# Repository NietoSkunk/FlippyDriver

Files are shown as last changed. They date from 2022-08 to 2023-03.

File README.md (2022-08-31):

# FlippyDriver

Driver board for Luminator MAX3000 Flip Dot Panels, allowing for chaining multiple panels, 3.3V and 5V tolerant inputs, and LED illumination with PWM dimming.

[Get it on PCBWay!](https://www.pcbway.com/project/shareproject/Luminator_MAX3000_Driver_Board_04b50fe9.html)

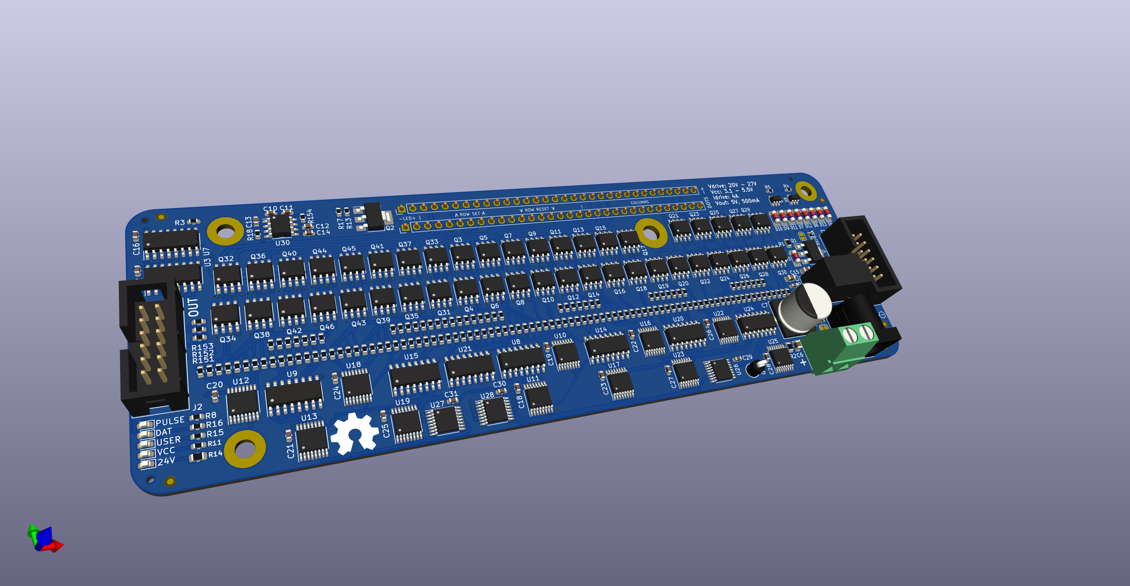
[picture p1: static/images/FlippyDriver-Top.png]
top

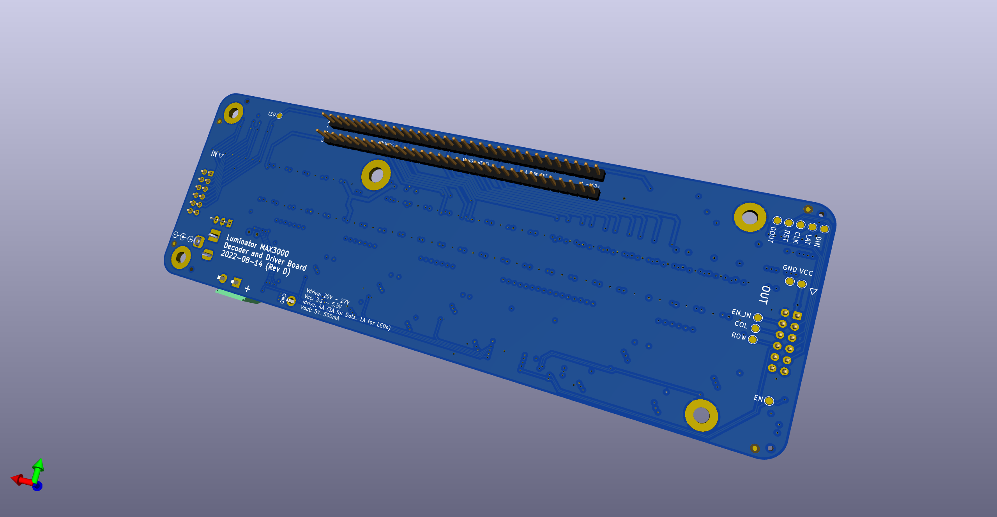
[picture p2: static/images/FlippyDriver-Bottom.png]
bottom

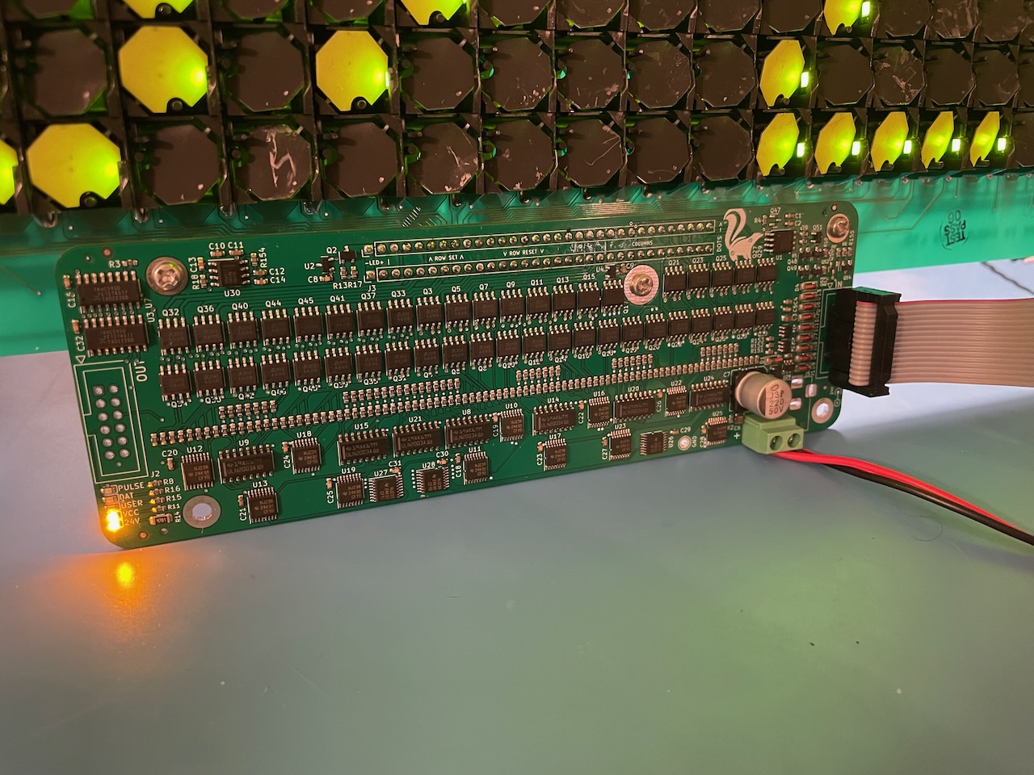
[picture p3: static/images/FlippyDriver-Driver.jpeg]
driver board

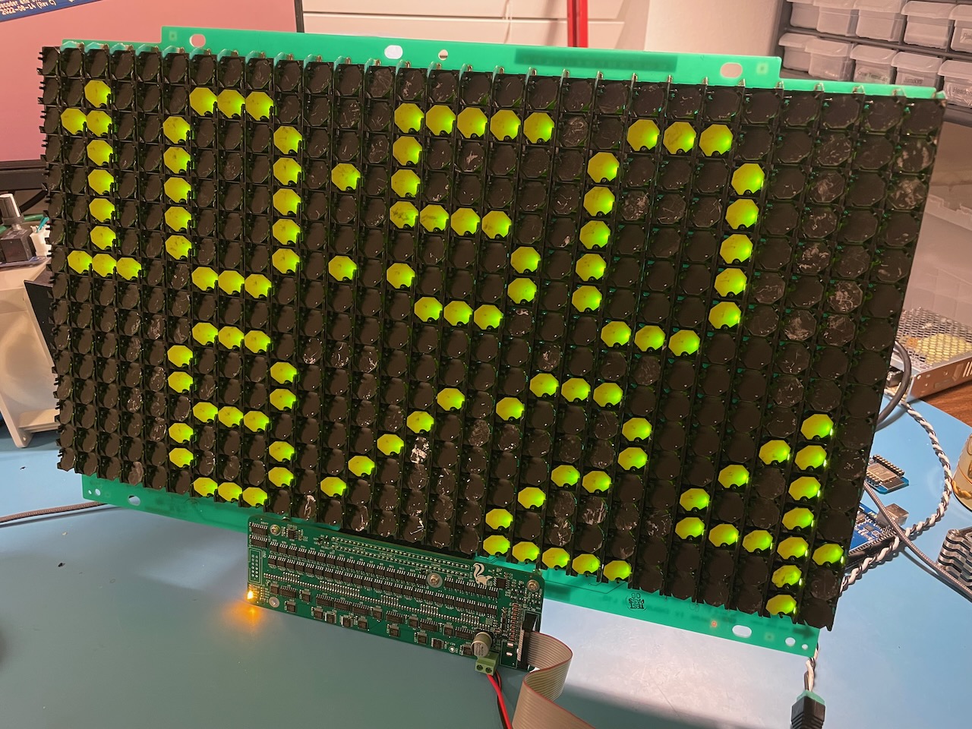
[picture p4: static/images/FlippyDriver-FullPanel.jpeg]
full panel


## Cloning repository (with Submodules)

```bash
$ git clone --recurse-submodules git@github.com:NietoSkunk/FlippyDriver.git
```

## Production notes

* 4 Layer board, preferably at least TG155. The display traces get warm when running at full tilt, and proper ventilation and thermal management is recommended.
* Several components are marked as DNI and are not necessary to populate. 
* F1, F2, and U30 have solder jumpers to bypass if they are not populated.
* Two mounting holes are in line with the holes on the panel, and support a 10mm M3 standoff. The larger mounting hole in the middle of the mouard matches with the hole on the panel, and supports a 10mm M4 standoff.
* The 7805 5V Aux Output is compatible with both a VX7805-500 switching regulator module and a L7805 linear regulator (heatsink recommended).

## Associated projects

* [FlippyAdapter - Panel Header to IDE Ribbon Cables](https://github.com/NietoSkunk/FlippyAdapter)
* [FlippyControl - Arduino / ESP32 Shield](https://github.com/NietoSkunk/FlippyControl)

## Data Harness

| Pin | # | # | Pin |
| --- | - | - | --- |
| VCC | 1 | 2 | GND |
| MOSI | 3 | 4 | PULSE_ENABLE |
| LATCH | 5 | 6 | COL_PULSE_N |
| CLK | 7 | 8 | ROW_PULSE_N |
| RESET | 9 | 10 | LED PWM |
| 5V Return | 11 | 12 | GND |

All logic circuitry is both 3.3V and 5V tolerant, as long as the VCC power rail is at least as high as the logic voltage. The RESET line has a pull-down resistor and is Active-Low. The PULSE_ENABLE pin is active high (i.e. pulse on high level), and the COL and ROW PULSE pins are active low (i.e. pulse on low level). 

WARNING: The low side sink drivers must be turned on after the high side, and turned off before the high side. For example, a pulse sequence of ROW Low, COL Low, COL High, ROW High would be used if the row is sourced and the column is grounded in order to set a bit. Damage may occur to the circuit if this order is not maintained!

The 5V Return pin is connected to the output of the 7805 regulator, which allows a board to receive 5V power from the 24V drive power.  It is not passed through to other modules, and thus only the first board in the chain has an accessible 5V output. All other boards in the chain do not have the aux output routed anywhere, and they can optionally be depopulated.

## Board Harness

| Pin | # | # | Pin |
| --- | - | - | --- |
| LED- | 1 | 2 | LED- |
| LED+ | 3 | 4 | LED+ |
| ROW_2_RESET | 5 | 6 | ROW_2_SET |
| ROW_4_RESET | 7 | 8 | ROW_4_SET |
| ROW_6_RESET | 9 | 10 | ROW_6_SET |
| ROW_8_RESET | 11 | 12 | ROW_8_SET |
| ROW_10_RESET | 13 | 14 | ROW_10_SET |
| ROW_12_RESET | 15 | 16 | ROW_12_SET |
| ROW_14_RESET | 17 | 18 | ROW_14_SET |
| ROW_16_RESET | 19 | 20 | ROW_16_SET |
| ROW_15_RESET | 21 | 22 | ROW_15_SET |
| ROW_13_RESET | 23 | 24 | ROW_13_SET |
| ROW_11_RESET | 25 | 26 | ROW_11_SET |
| ROW_9_RESET | 27 | 28 | ROW_9_SET |
| ROW_7_RESET | 29 | 30 | ROW_7_SET |
| ROW_5_RESET | 31 | 32 | ROW_5_SET |
| ROW_3_RESET | 33 | 34 | ROW_3_SET |
| ROW_1_RESET | 35 | 36 | ROW_1_SET |
| COL_2 | 37 | 38 | COL_1 |
| COL_4 | 39 | 40 | COL_3 |
| COL_6 | 41 | 42 | COL_5 |
| COL_8 | 43 | 44 | COL_7 |
| COL_10 | 45 | 46 | COL_9 |
| COL_12 | 47 | 48 | COL_11 |
| COL_14 | 49 | 50 | COL_13 |
| COL_16 | 51 | 52 | COL_15 |
| COL_18 | 53 | 54 | COL_17 |
| COL_20 | 55 | 56 | COL_19 |
| COL_22 | 57 | 58 | COL_21 |
| COL_24 | 59 | 60 | COL_23 |
| COL_26 | 61 | 62 | COL_25 |
| COL_28 | 63 | 64 | COL_27 |

## LEDs

  * PULSE: Illuminated when the PULSE_ENABLE pin is high.
  * DAT: Illuminates when data is being clocked into the shift register.
  * USER: Programmable LED connected to bit 12 of the shift register.
  * VCC: Illuminated when the VCC power rail is present.
  * 24V: Illuminated when the 24V power rail is present.

## Shift Register

Each board contains a pair of 74HC595 shift registers, which are used to select a single pixel to be enabled at a time. This can be driven either directly with GPIO outputs, or using a hardware SPI output. The format of the data is MSB first, clock on high.

The Row and Column decoders are grouped into banks of eight, using 74HC238 3:8 decoders. The Column and Row A2/A1/A0 lines select the output of each bank, and the Column and Row Bank lines select which bank is active. The Row and Column source line switches that output to drive a high side source instead of a low side sink.

The I2C Pullup line is used to enable a set of 4.7kOhm resistors on the I2C bus, which allows a single board in a chain to optionally provide pullups.

The output of the shift register is sent out to the OUT header, and comes in to the next board in the chain on the MOSI line. This allows multiple boards to be controlled at once by shifting 16 bits of data for each board.

| Bit | Function |
| --- | --- |
|  0  | Column A2 |
|  1  | Column A1 |
|  2  | Column A0 |
|  3  | Row A0 |
|  4  | Row A1 |
|  5  | Row A2 |
|  6  | Row Bank |
|  7  | Column Bank 0 |
|  8  | Column Source |
|  9  | N/C |
|  10 | Row Source |
|  11 | Row Bank |
|  12 | N/C |
|  13 | User LED |
|  14 | N/C |
|  15 | N/C |

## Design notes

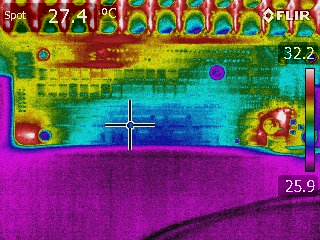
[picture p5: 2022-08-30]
static/images/Thermals_1.jpg

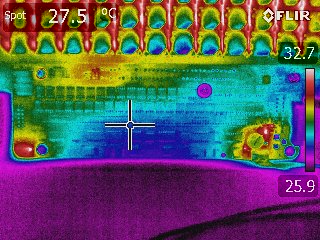
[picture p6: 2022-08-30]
static/images/Thermals_2.jpg

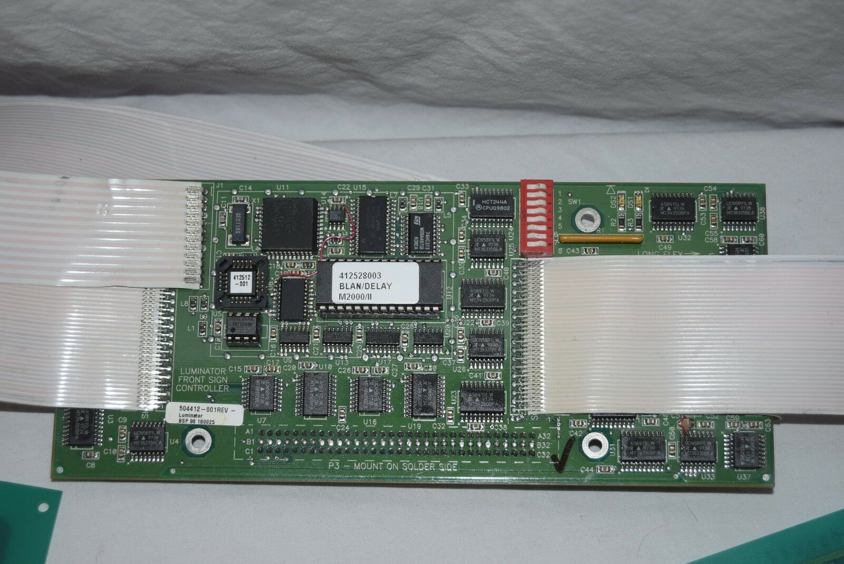
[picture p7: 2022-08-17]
Reference/s-l1600.jpg

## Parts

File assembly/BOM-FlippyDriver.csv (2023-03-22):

Comment | Designator | Footprint | LCSC
220u | C4 | CP_Elec_10x10 | C125977
0.1u | C10,C16,C18,C19,C2,C20,C21,C22,C23,C24,C25,C26,C27,C28,C29,C30,C31,C32,C33,C36,C37,C38,C5,C6,C7,C9 | C_0603_1608Metric | C14663
AO3401A | Q1,Q2,Q47,Q48,Q53 | SOT-23 | C15127
1u | C11,C12,C34 | C_0603_1608Metric | C15849
10k | R14,R3,R9 | R_0805_2012Metric | C17414
500mA | F2 | Fuse_0603_1608Metric | C206959
AO3400A | Q49,Q50,Q51,Q52,Q54,Q55 | SOT-23 | C20917
1k | R100,R101,R102,R119,R120,R121,R122,R123,R124,R125,R126,R13,R143,R144,R145,R146,R147,R148,R149,R150,R153,R35,R36,R37,R38,R39,R40,R41,R42,R59,R60,R61,R62,R63,R64,R65,R66,R83,R84,R85,R86,R87,R88,R89,R90,R99 | R_0603_1608Metric | C21190
2.4k,1% | R12,R159,R160 | R_0603_1608Metric | C22940
220R | R11,R15,R2,R8 | R_0603_1608Metric | C22962
5.6k,1% | R16 | R_0603_1608Metric | C23189
56k | R1,R10,R17,R4,R5,R6,R7 | R_0603_1608Metric | C23206
10k | R103,R104,R105,R106,R107,R108,R109,R110,R111,R112,R113,R114,R115,R116,R117,R118,R127,R128,R129,R130,R131,R132,R133,R134,R135,R136,R137,R138,R139,R140,R141,R142,R151,R152,R154,R155,R156,R157,R158,R161,R18,R19,R20,R21,R22,R23,R24,R25,R26,R27,R28,R29,R30,R31,R32,R33,R34,R43,R44,R45,R46,R47,R48,R49,R50,R51,R52,R53,R54,R55,R56,R57,R58,R67,R68,R69,R70,R71,R72,R73,R74,R75,R76,R77,R78,R79,R80,R81,R82,R91,R92,R93,R94,R95,R96,R97,R98 | R_0603_1608Metric | C25804
1u | C1 | C_0805_2012Metric | C28323
4.7u | C8 | C_1206_3216Metric | C29823
SMAJ33CA | D5 | D_SMA | C3019524
CJ431 | U2 | SOT-23 | C3113
AP4606 | Q10,Q11,Q12,Q13,Q14,Q15,Q16,Q17,Q18,Q19,Q20,Q21,Q22,Q23,Q24,Q25,Q26,Q27,Q28,Q29,Q3,Q30,Q31,Q32,Q33,Q34,Q35,Q36,Q37,Q38,Q39,Q4,Q40,Q41,Q42,Q43,Q44,Q45,Q46,Q5,Q6,Q7,Q8,Q9 | SOIC-8_3.9x4.9mm_P1.27mm | C353084
74HC238 | U10,U11,U12,U13,U16,U17,U18,U19,U22,U23,U25,U26,U27,U28 | TSSOP-16_4.4x5mm_P0.65mm | C403724
MCP9700T-ETT | U29,U6 | SOT-23 | C42288
10u | C15,C17,C3,C35 | C_0805_2012Metric | C440198
5A | F1 | Fuse_0603_1608Metric | C553915
0.01u | C13,C14 | C_0603_1608Metric | C57112
74HC595 | U3,U7 | SOIC-16_3.9x9.9mm_P1.27mm | C5947
19-213/Y2C-CQ2R2L/3T(CY) | D14,D3 | LED_0603_1608Metric | C72038
19-217/BHC-ZL1M2RY/3T | D15 | LED_0603_1608Metric | C72041
19-217/GHC-YR1S2/3T | D2 | LED_0603_1608Metric | C72043
ULN2003ADR | U14,U15,U20,U21,U24,U8,U9 | SOIC-16_3.9x9.9mm_P1.27mm | C7512
NE555D | U30 | SOIC-8_3.9x4.9mm_P1.27mm | C7593
LM393 | U1,U5 | SOIC-8_3.9x4.9mm_P1.27mm | C7955
ZMM5V6 | D1,D10,D11,D12,D13,D16,D17,D4,D6,D7,D8,D9 | D_MiniMELF | C8062
NCD0805R1 | D18 | LED_0805_2012Metric | C84256
MountingHole_Pad | H1 | MountingHole_3.5mm_Pad_TopBottom
MountingHole_Pad | H2 | MountingHole_3.5mm_Pad_TopBottom
MountingHole_Pad | H4 | MountingHole_3.5mm_Pad_TopBottom
MountingHole_Pad | H5 | MountingHole_4.5mm_Pad_TopBottom
MountingHole_Pad | H3 | MountingHole_3.5mm_Pad_TopBottom
24V Input | J5 | BarrelJack_Horizontal
GND | TP6 | TestPoint_Keystone_5005-5009_Compact
Board Harness | J3 | Luminator_MAX3000
Data Harness In | J1 | IDC-Header_2x06_P2.54mm_Vertical
Data Harness Out | J2 | IDC-Header_2x06_P2.54mm_Vertical
LAT | TP12 | TestPoint_Pad_D1.5mm
DIN | TP11 | TestPoint_Pad_D1.5mm
COL | TP15 | TestPoint_Pad_D1.5mm
RST | TP2 | TestPoint_Pad_D1.5mm
VCC | TP4 | TestPoint_Pad_D1.5mm
EN | TP13 | TestPoint_Pad_D1.5mm
EN_IN | TP7 | TestPoint_Pad_D1.5mm
ROW | TP14 | TestPoint_Pad_D1.5mm
DOUT | TP3 | TestPoint_Pad_D1.5mm
CLK | TP1 | TestPoint_Pad_D1.5mm
GND | TP5 | TestPoint_Pad_D1.5mm
LED | TP10 | TestPoint_Pad_D1.5mm
VX7805-500 | U4 | Converter_DCDC_RECOM_R-78E-0.5_THT
24V Input | J4 | TerminalBlock_Phoenix_MKDS-1,5-2_1x02_P5.00mm_Horizontal

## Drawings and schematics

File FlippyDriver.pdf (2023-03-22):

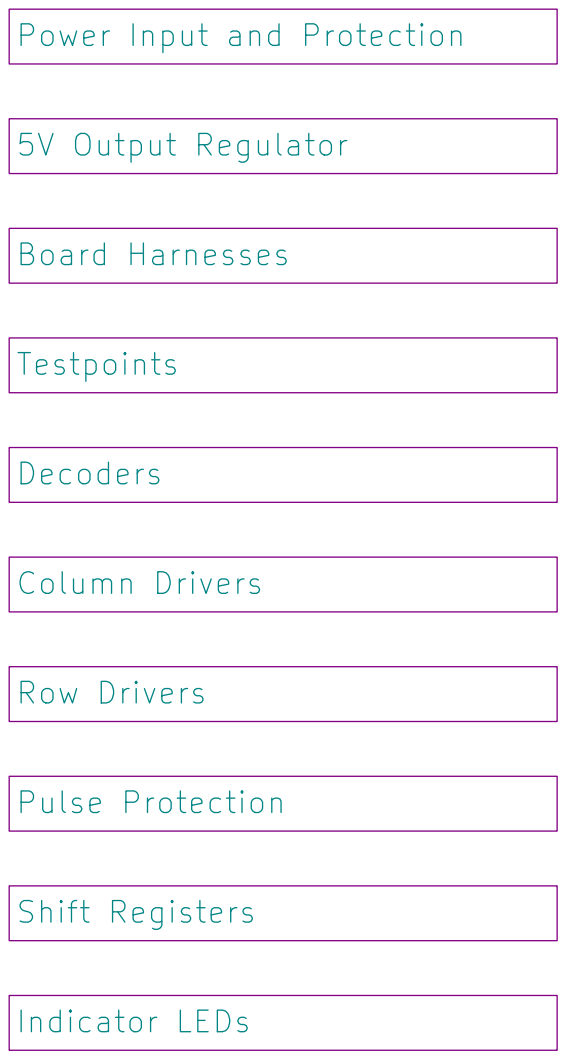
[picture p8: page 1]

Power Input and Protection

File: FlippyDriver.kicad_sch Sheet: / Row Drivers

Id: 1/11 Title: Luminator MAX3000 Custom Driver Board

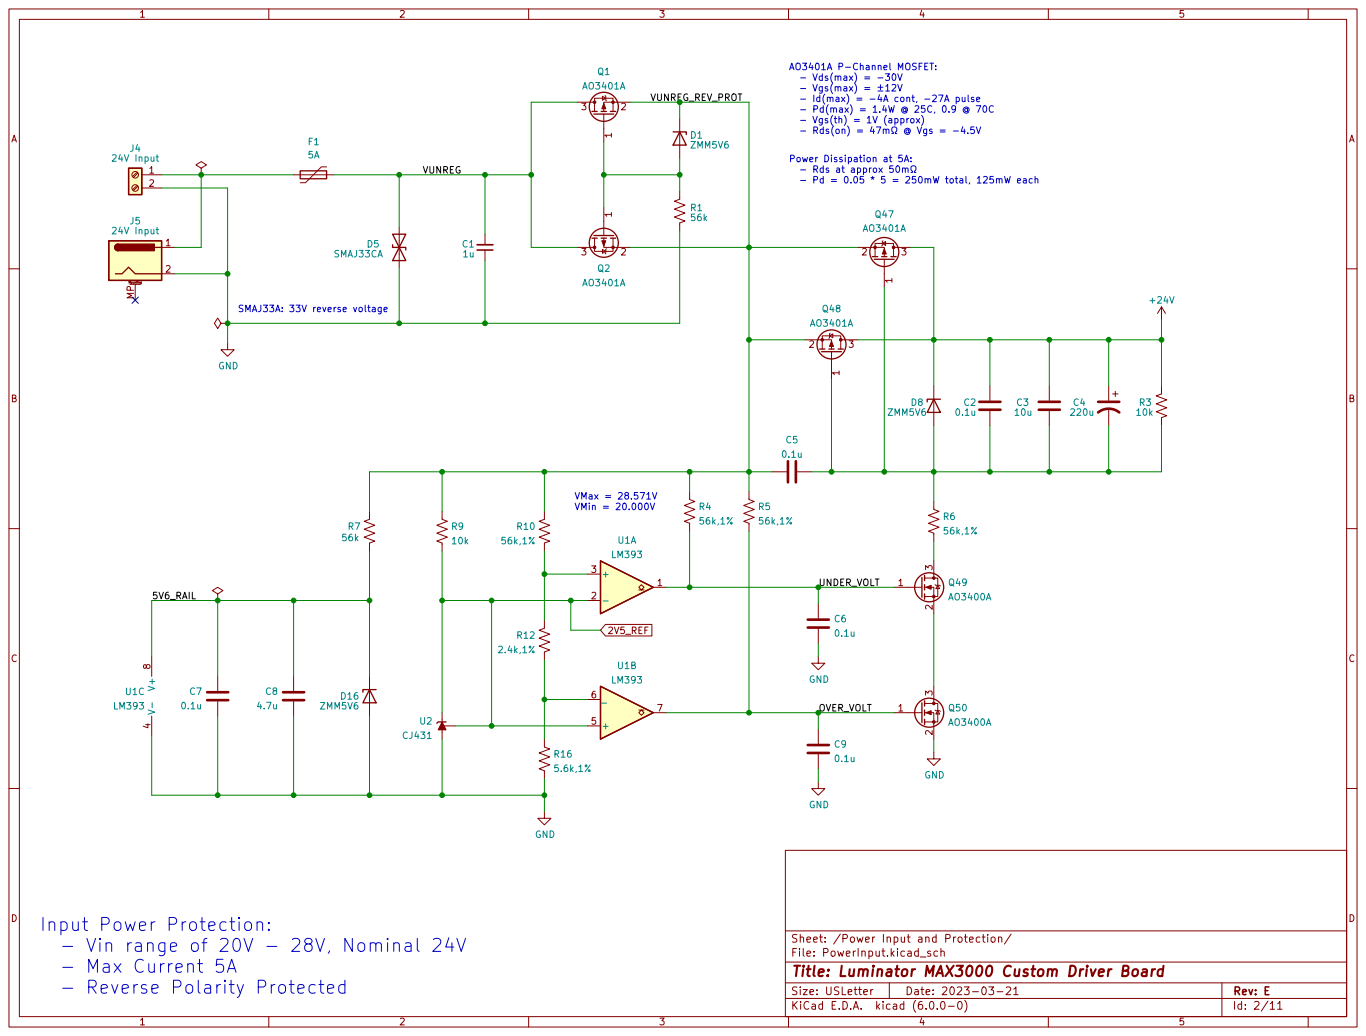
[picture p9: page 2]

- Vds(max) = -30V
- Id(max) = -4A cont, -27A pulse
- Pd(max) = 1.4W @ 25C, 0.9 @ 70C
- Vgs(th) = 1V (approx)

Sheet: /Power Input and Protection/ C6
0.1u GND

Input Power Protection:
- Vin range of 20V - 28V, Nominal 24V
- Max Current 5A
- Reverse Polarity Protected

File: PowerInput.kicad_sch
Id: 2/11 Title: Luminator MAX3000 Custom Driver Board

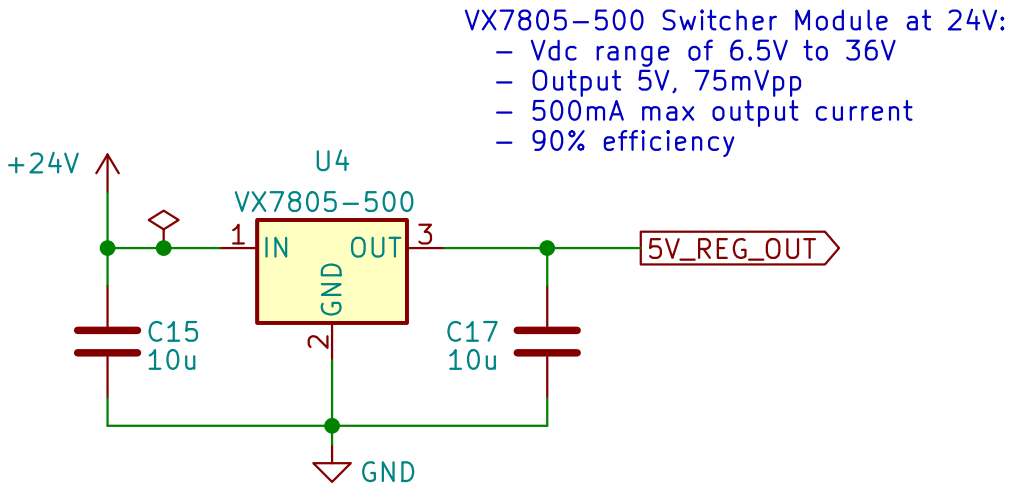
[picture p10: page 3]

5V_REG_OUT VX7805-500 Switcher Module at 24V:
- Vdc range of 6.5V to 36V
- Output 5V, 75mVpp
- 500mA max output current
- 90% efficiency

Sheet: /5V Output Regulator/ GND

File: 5V_Reg.kicad_sch
Id: 3/11 Title: Luminator MAX3000 Custom Driver Board

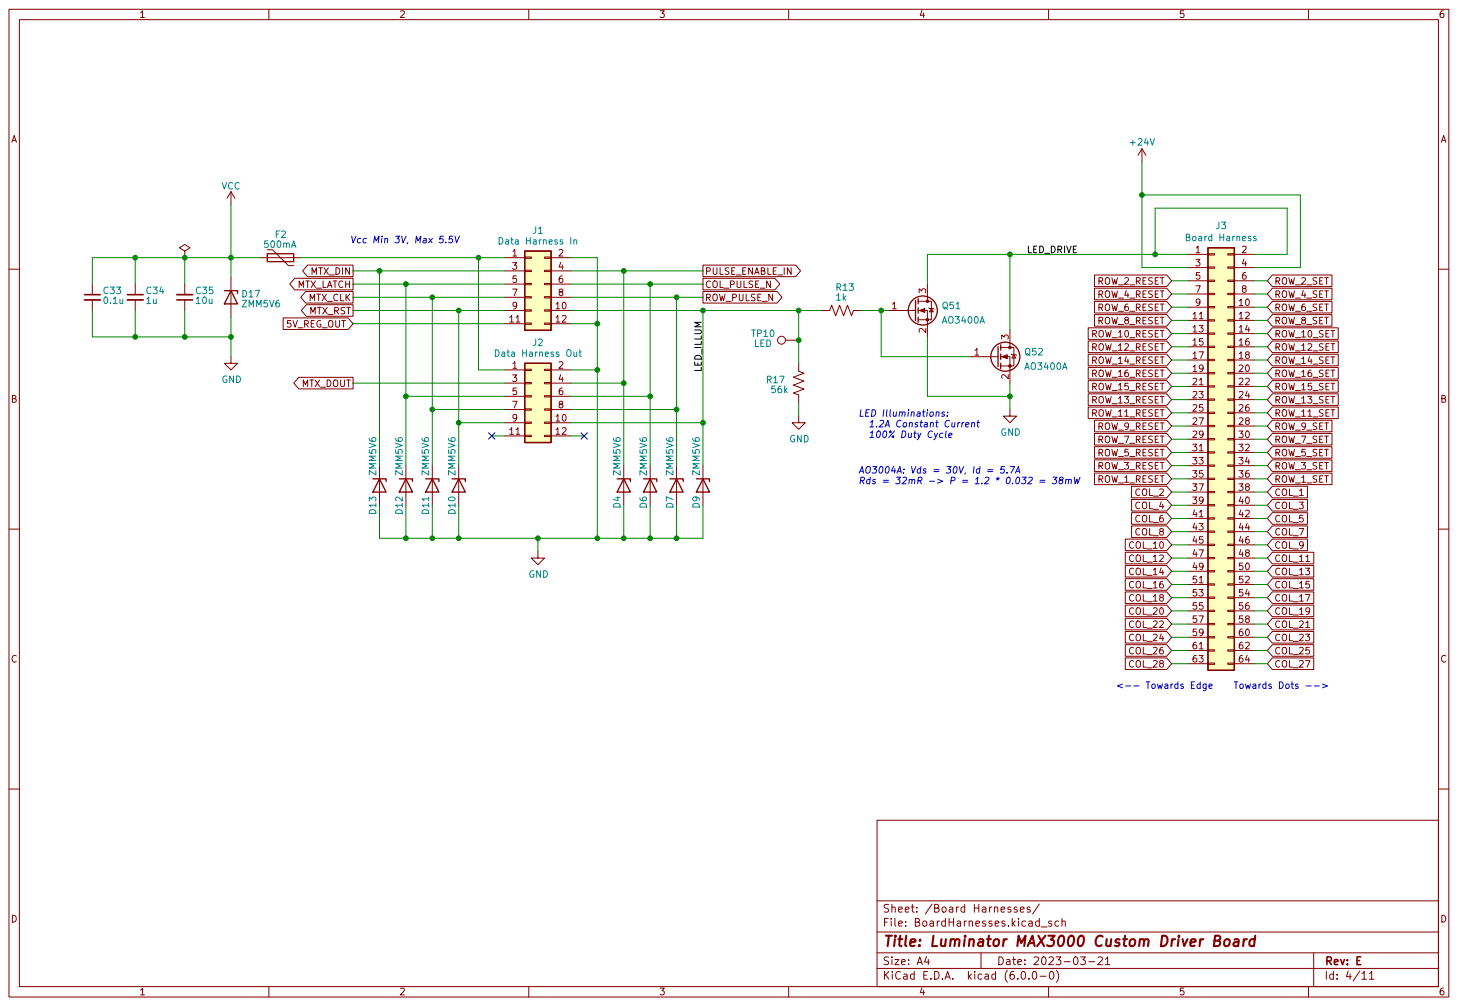
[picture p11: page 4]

9 | | 10

File: BoardHarnesses.kicad_sch Sheet: /Board Harnesses/ GND

<-- Towards Edge Towards Dots -->

Id: 4/11 Title: Luminator MAX3000 Custom Driver Board

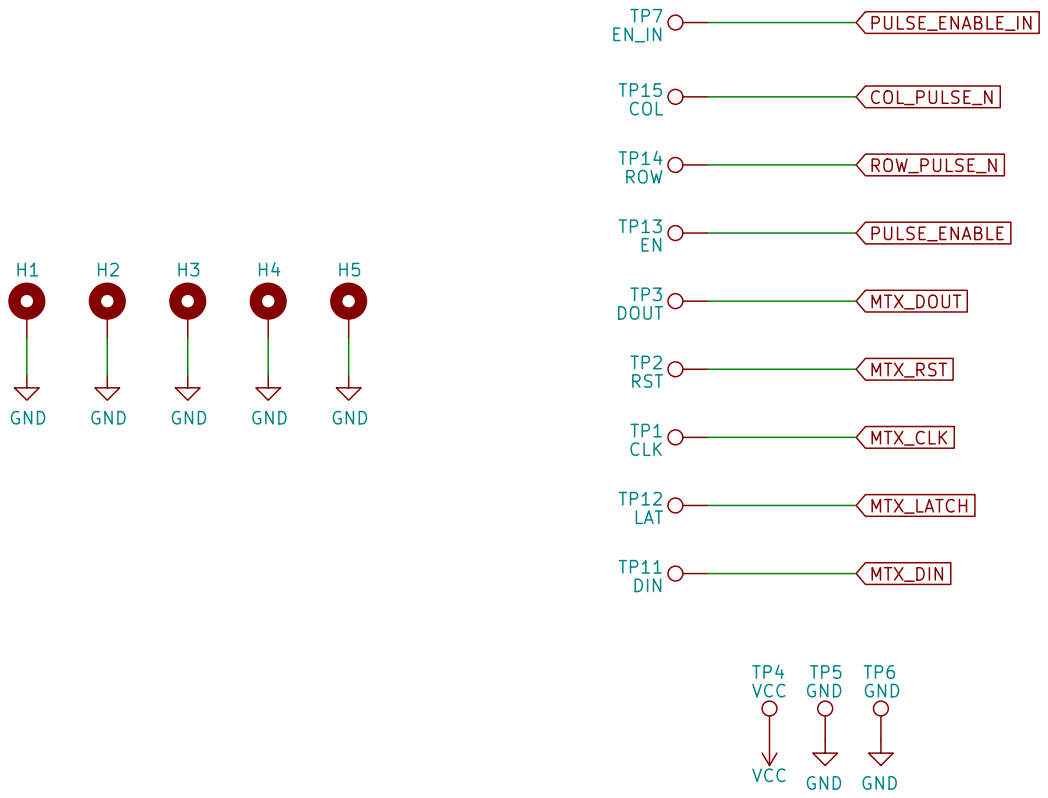
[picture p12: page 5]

Sheet: /Testpoints/
File: Testpoints.kicad_sch
Id: 5/11 Title: Luminator MAX3000 Custom Driver Board

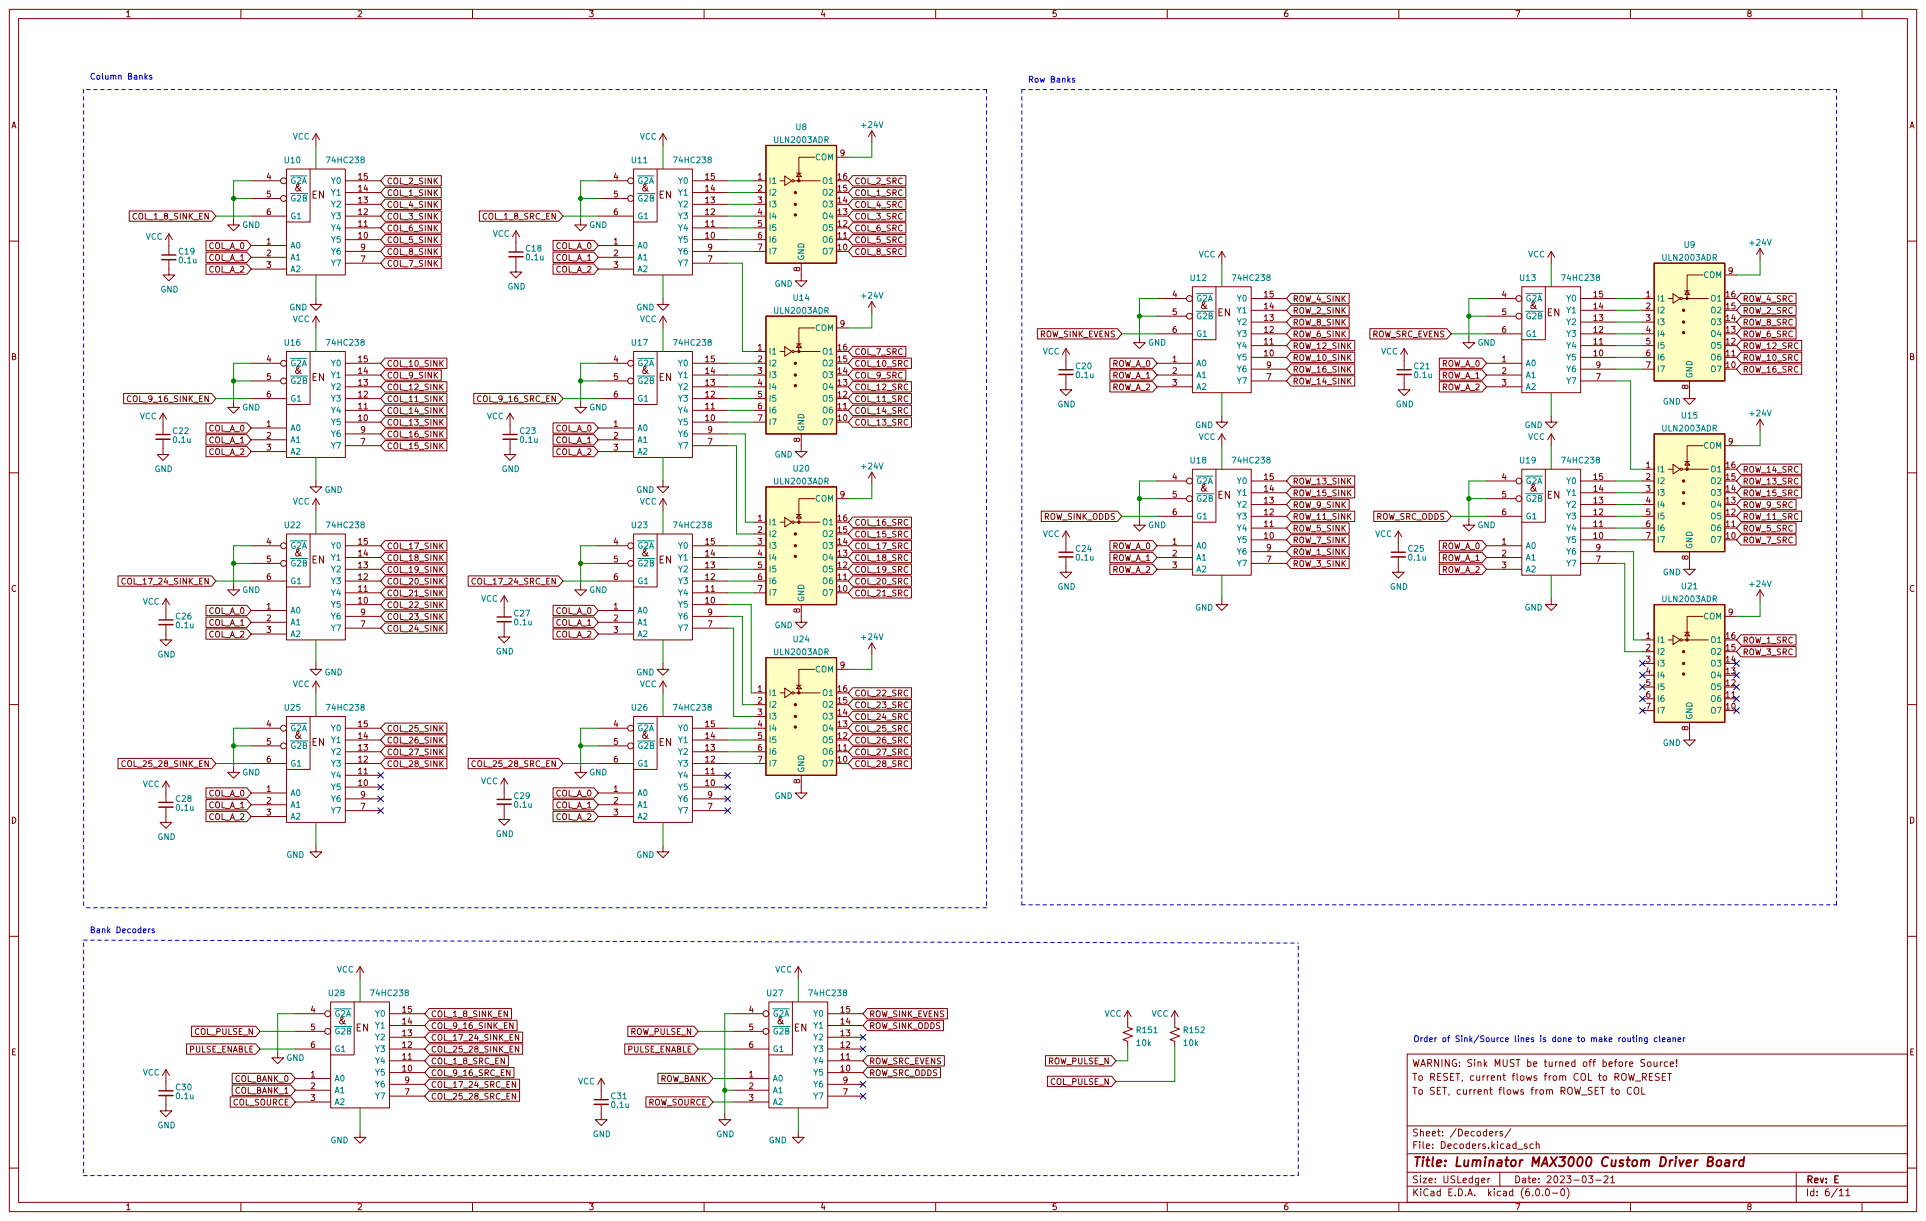
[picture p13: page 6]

ROW_A_0 Order of Sink/Source lines is done to make routing cleaner Bank Decoders

E Date: 2023-03-21 KiCad E.D.A. kicad (6.0.0-0)
To RESET, current flows from COL to ROW_RESET WARNING: Sink MUST be turned off before Source!

File: Decoders.kicad_sch Sheet: /Decoders/ To SET, current flows from ROW_SET to COL

Id: 6/11 Title: Luminator MAX3000 Custom Driver Board

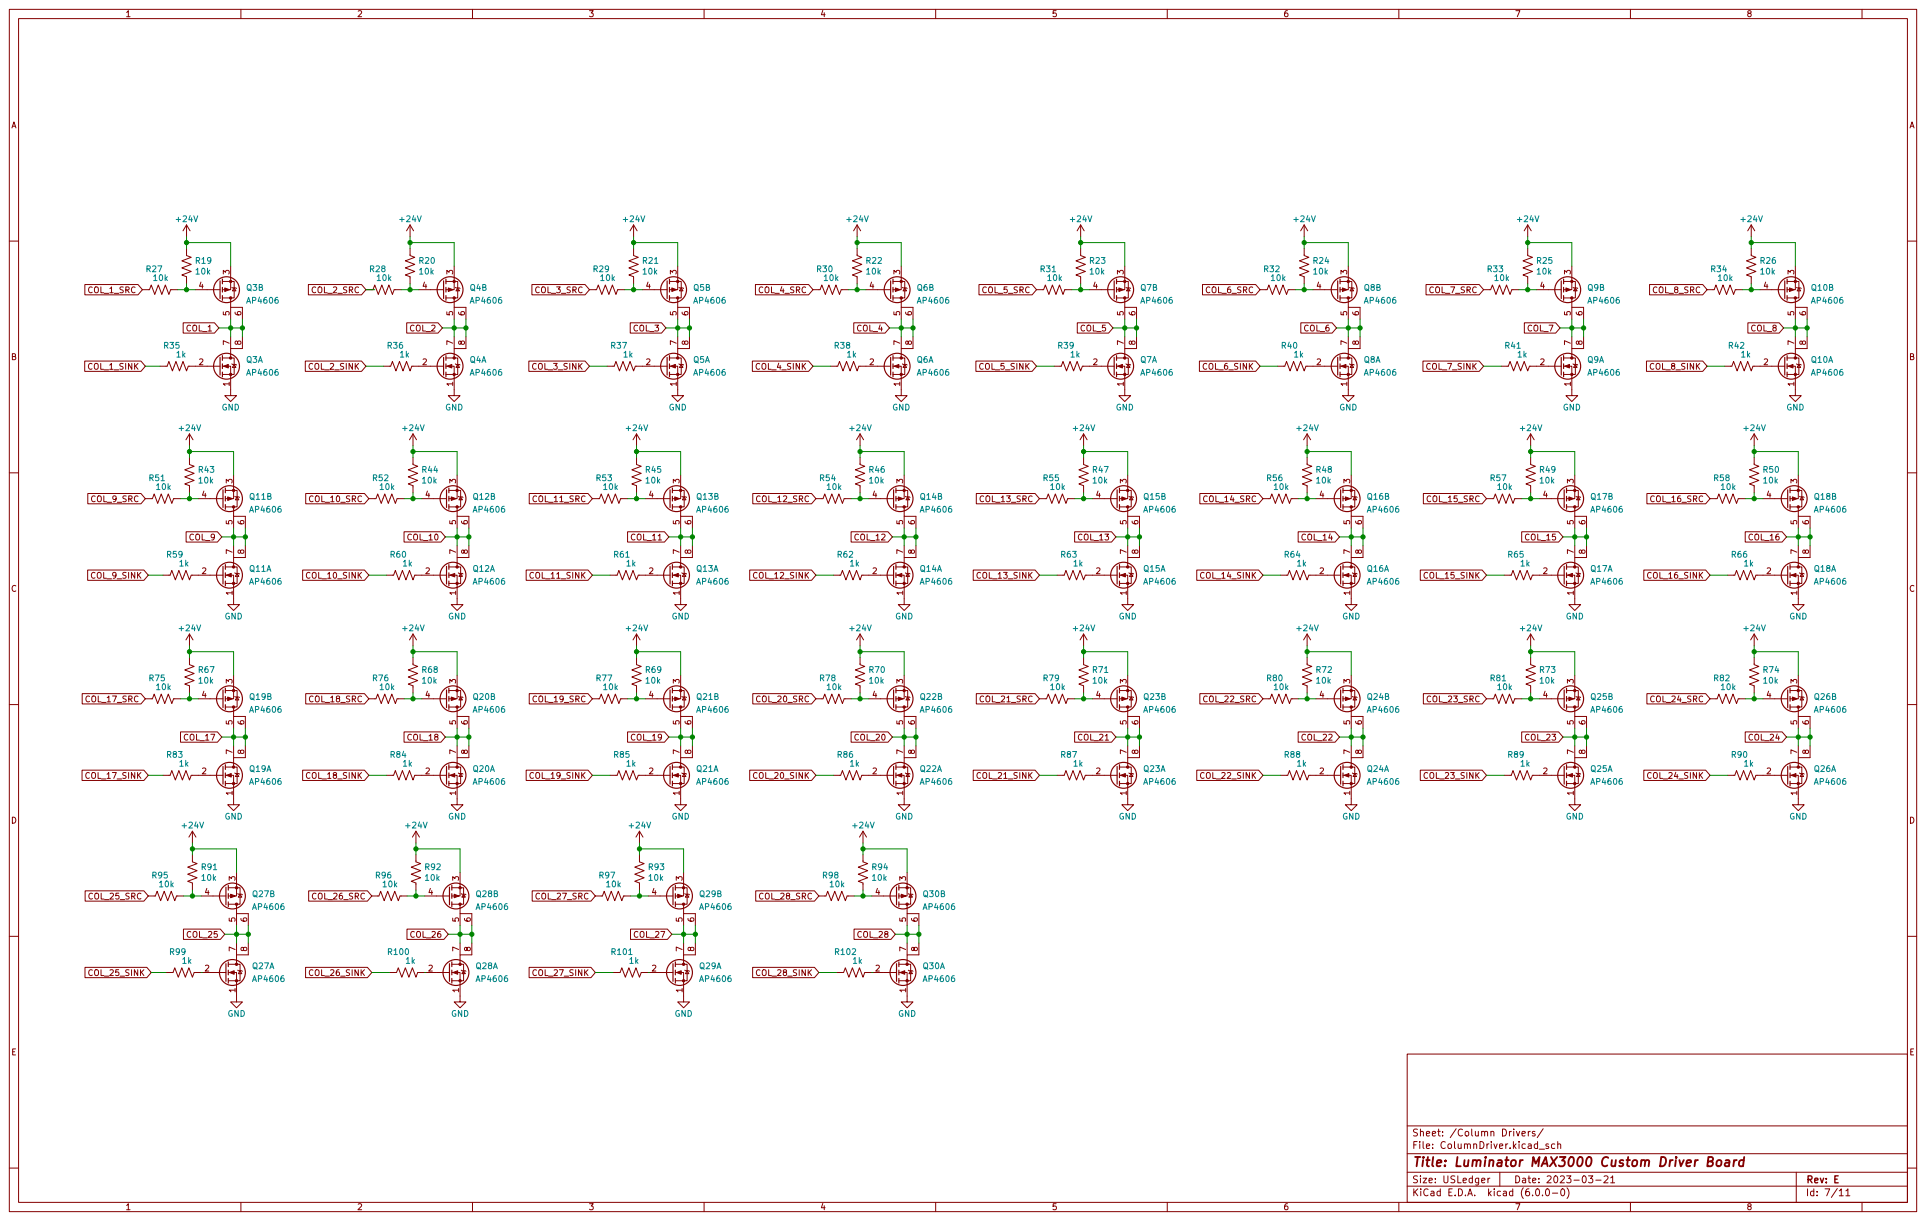
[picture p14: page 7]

File: ColumnDriver.kicad_sch Sheet: /Column Drivers/ 1

Id: 7/11 Title: Luminator MAX3000 Custom Driver Board

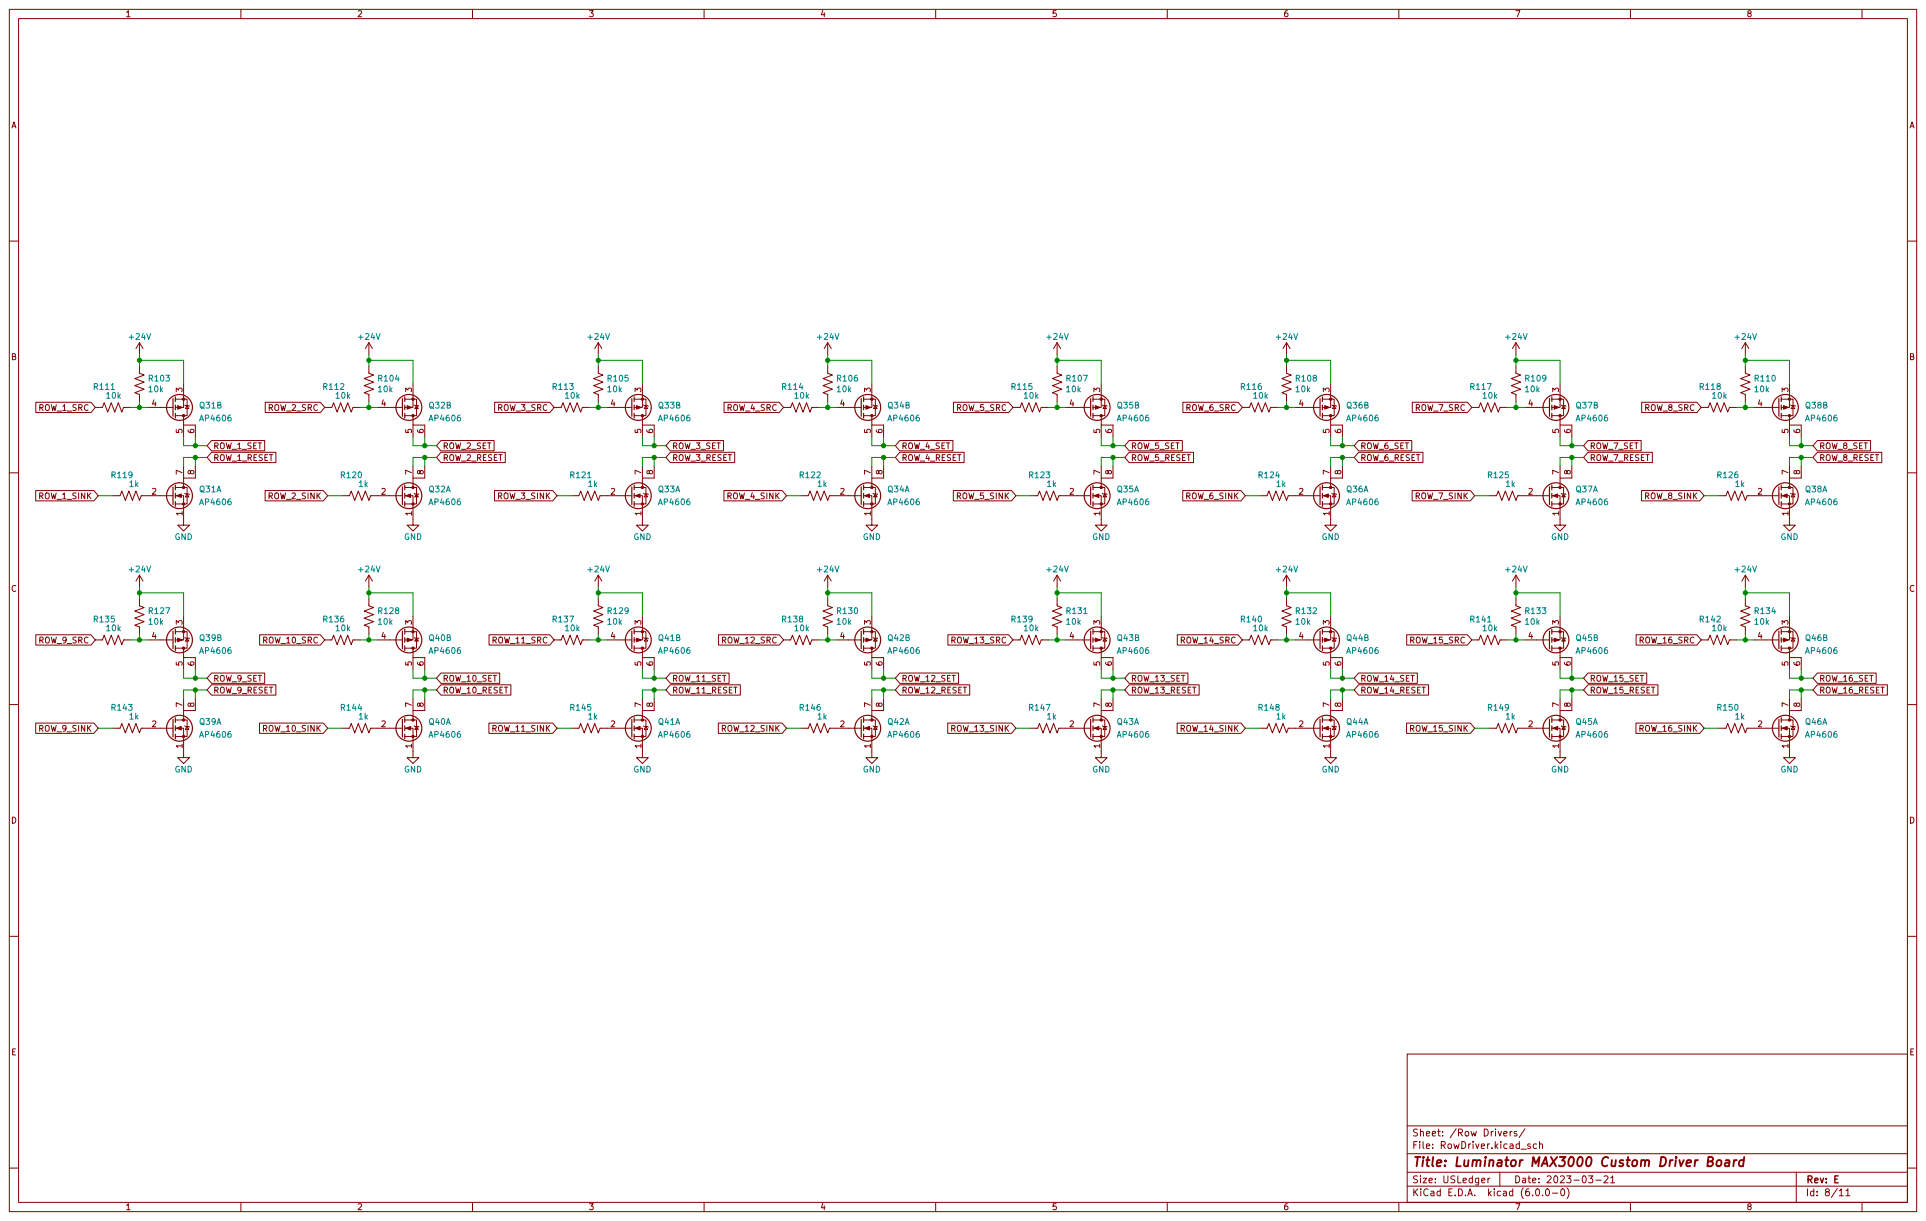
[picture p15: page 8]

File: RowDriver.kicad_sch Sheet: /Row Drivers/
Id: 8/11 Title: Luminator MAX3000 Custom Driver Board

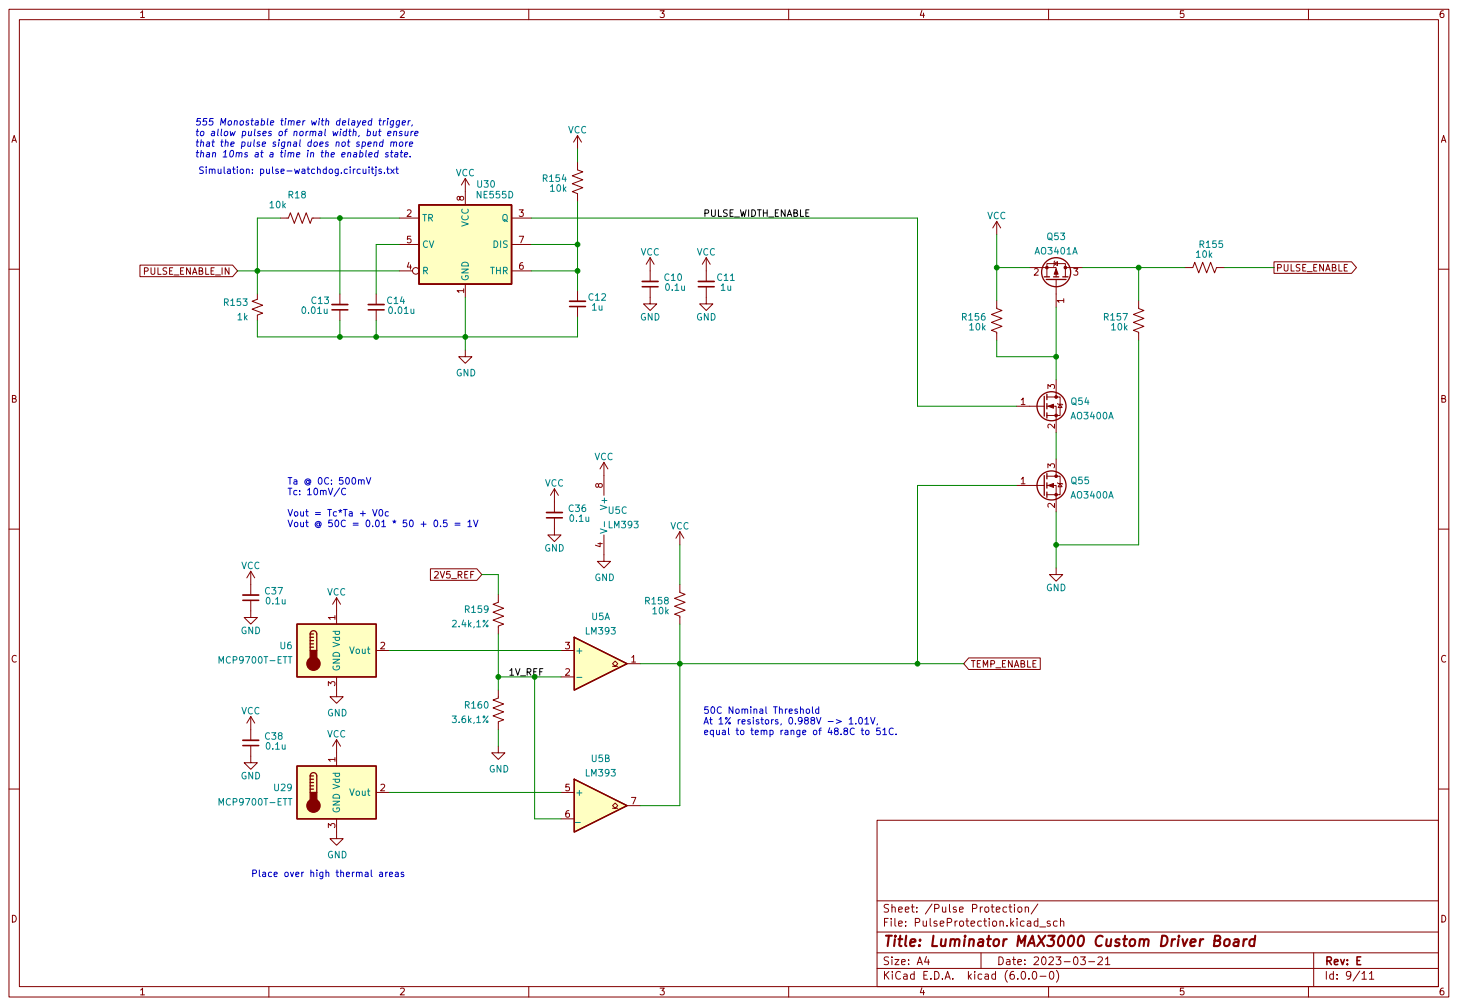
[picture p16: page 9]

555 Monostable timer with delayed trigger,
to allow pulses of normal width, but ensure
that the pulse signal does not spend more
than 10ms at a time in the enabled state.
Simulation: pulse-watchdog.circuitjs.txt
0.01u GND

Vout = Tc*Ta + V0c Vout @ 50C = 0.01 * 50 + 0.5 = 1V

50C Nominal Threshold At 1% resistors, 0.988V -> 1.01V, equal to temp range of 48.8C to 51C.

Place over high thermal areas

File: PulseProtection.kicad_sch Sheet: /Pulse Protection/
Id: 9/11 Title: Luminator MAX3000 Custom Driver Board

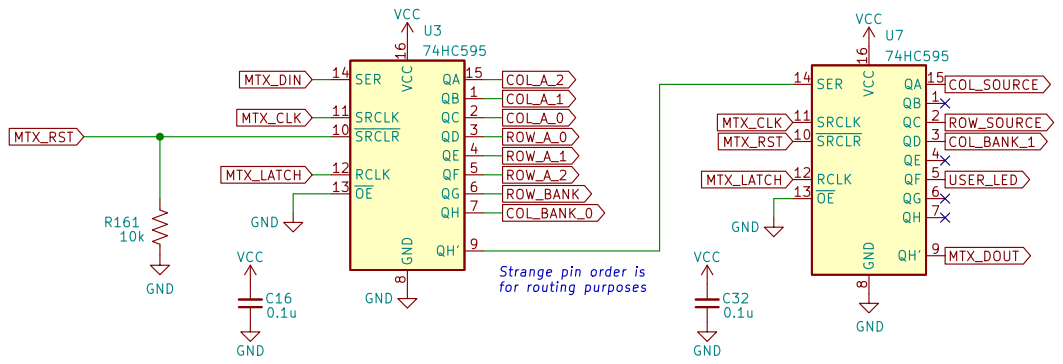
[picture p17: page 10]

File: ShiftRegisters.kicad_sch
Id: 10/11 Title: Luminator MAX3000 Custom Driver Board

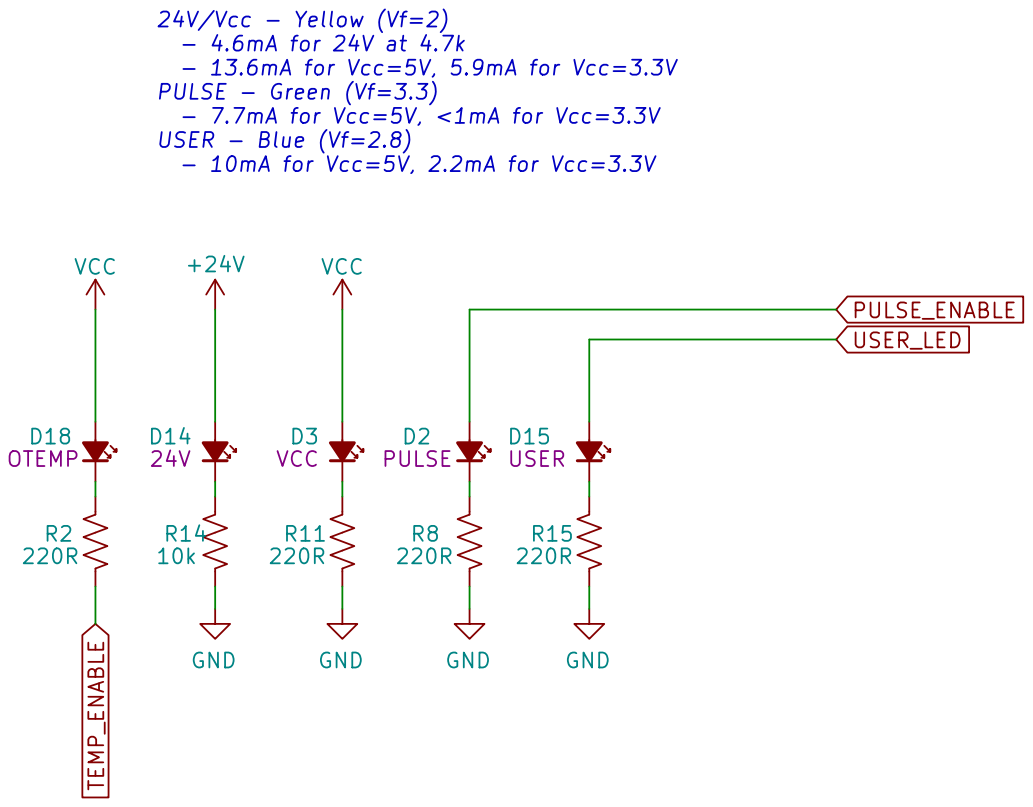
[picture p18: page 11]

24V/Vcc - Yellow (Vf=2)
- 4.6mA for 24V at 4.7k
- 13.6mA for Vcc=5V, 5.9mA for Vcc=3.3V
PULSE - Green (Vf=3.3)
- 7.7mA for Vcc=5V, <1mA for Vcc=3.3V USER - Blue (Vf=2.8)

- 10mA for Vcc=5V, 2.2mA for Vcc=3.3V

File: Indicators.kicad_sch Sheet: /Indicator LEDs/
Id: 11/11 Title: Luminator MAX3000 Custom Driver Board

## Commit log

2022-08-17 Commit Rev C of Flippy Driver
    [ColumnDriver.kicad_sch, Decoders.kicad_sch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]
2022-08-25 Add subrevision, reference submodule objects
    [BOM-FlippyDriver.csv, ColumnDriver.kicad_sch, Decoders.kicad_sch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]
2022-08-25 Add images and 3D models
    [ColumnDriver.kicad_sch, FlippyDriver.kicad_sch, RowDriver.kicad_sch]
2022-08-25 Update Gerbers and PCBA
    [BOM-FlippyDriver.csv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]
2022-08-25 Add more wiring details to README
2022-08-30 Initial draft of Revision D
    - Remove I2C Bus, and replace with PWM Input
    - Remove temp sensors due to no I2C bus
    - Add 5V aux output from 24V, supports LM7805 (w/ Heatsink) and VX7805
    - Larger components for high current nets
    [BOM-FlippyDriver.csv, ColumnDriver.kicad_sch, Decoders.kicad_sch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]
2022-08-31 Finalize Revision D
    [BOM-FlippyDriver.csv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]
2022-08-31 Add link to PCBWay
2022-12-01 Replace out of stock parts with current JLCPCB parts
    [BOM-FlippyDriver.csv, ColumnDriver.kicad_sch, Decoders.kicad_sch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]
2023-03-07 Replace LCSC parts with ones in stock
    [BOM-FlippyDriver.csv, Decoders.kicad_sch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]
2023-03-22 Revision E, adds voltage bounding and thermal protection
    [5V_Reg.kicad_sch, BOM-FlippyDriver.csv, BoardHarnesses.kicad_sch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]
